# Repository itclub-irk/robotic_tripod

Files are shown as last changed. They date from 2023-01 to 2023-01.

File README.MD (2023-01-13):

# Роботизированный штатив

Данное устройство позволяет осуществлять наведение закрепленного на поворотном штативе прибора (камера, антенна, фонарь и т.д.) на портативный радиомаяк.

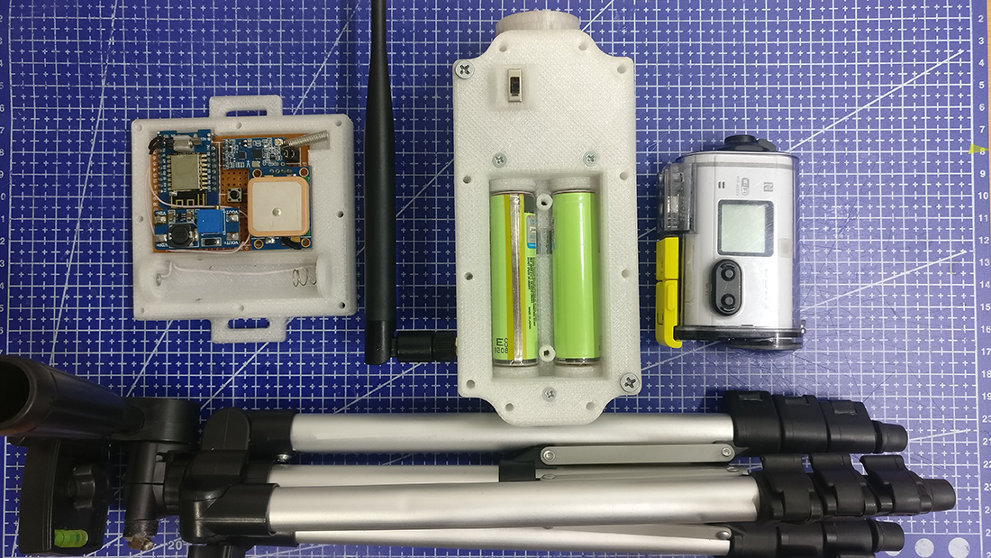
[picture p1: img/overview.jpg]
Внешний вид штатива


<details>
  <summary>Демонстрация работы штатива (18 Мб)</summary>

Демонстрация работы штатива

</details>

## Краткое описание конструкции

Штатив состоит из двух компонент - поворотный механизм и радиомаяк.

Радиомаяк определяет угловое положение относительно штатива при помощи ГНСС-приемника. Вычисленное значение при помощи беспроводного канала связи передаётся в поворотный механизм.

Поворотный механизм осуществляет поворот платформы с закрепленным прибором на требуемый угол.

## Варианты реализации

В данном репозитории представлен исходный код различных вариантов реализации роботизированного штатива.

Варианты поворотного механизма:

- С приводом платформы от сервопривода с PWM интерфейсом (Например SG90);
- С приводом от биполярного шагового двигателя NEMA с драйвером, поддерживающим интерфейс STEP/DIR (использовался двигатель NEMA17 и драйвер TMC2130);
- С приводом от униполярного шагового двигателя 28byj-48 и буфером ULN2003.
- С релейным трехпозиционным регулятором;
- С ПИД регулятором.

Варианты радиомаяка:

- С использованием библиотеки
  NeoGPS и аппаратного UART;
- С использованием библиотеки TinyGPS и программного UART для подключения к ГНСС-приёмнику;
- С использованием UART трансиверов HC-12 и программным контролем целостности пакетов;
- С использованием SPI трансиверов sx1278 на базе технологии LoRa и программным контролем целостности пакетов;
- С использованием UART трансиверов Ebyte E32-868T20S на базе технологии LoRa и аппаратным контролем целостности пакетов;
- Без внешних радиомодулей, с использованием AdHoc WiFi, UDP-датаграм и программным контролем целостности пакетов;
- Без внешних радиомодулей, с использованием протокола ESP-Now и программным контролем целостности пакетов;
- С обратной связью с поворотным механизмом;
- Без обратной связи с поворотным механизмом.

## Аппаратное обеспечение

Поворотный механизм (в зависимости от выбранного варианта реализации):

- WeMos D1 mini (ESP8266/ESP8266Ex);
- HC-12/SX1278/E32-868T20S
- Sg90/28byj-48/NEMA17
- ULN2003/TMC2130;
- Микропереключатель;
- Li-ION АКБ типоразмера 18650 (2 шт.);
- Понижающий DCDC преобразователь 8.2 ... 7.4 -> 5в;
- Внешняя штырьевая антенна на выбранный диапазон частот;
- Коаксиальный кабель с волновым сопротивлением 50 Ом и коннекторы для подключения кабеля к антенне и выбранному трансиверу.

Радиомаяк (В зависимости от выбранного варианта реализации):

- WeMos D1 mini (ESP8266/ESP8266Ex);
- HC-12/SX1278/E32-868T20S
- ГНСС-приемник NEO-6M с UART интерфейсом;
- Миниатюрный вибромотор;
- Li-ION АКБ типоразмера 18650 (1 шт.);
- Повышающий DCDC-преобразователь 4.2 ... 2.7 -> 5в. (Опционально);
- Микрокнопка без фиксации;
- Спиральная антенна на выбранный диапазон частот.

Электронные компоненты располагаются на макетных платах. Платы и остальные элементы размещаются в печатных корпусах. Файлы для печати находятся в каталоге _3d_.

<details>
  <summary>Образцы моделей для печати</summary>

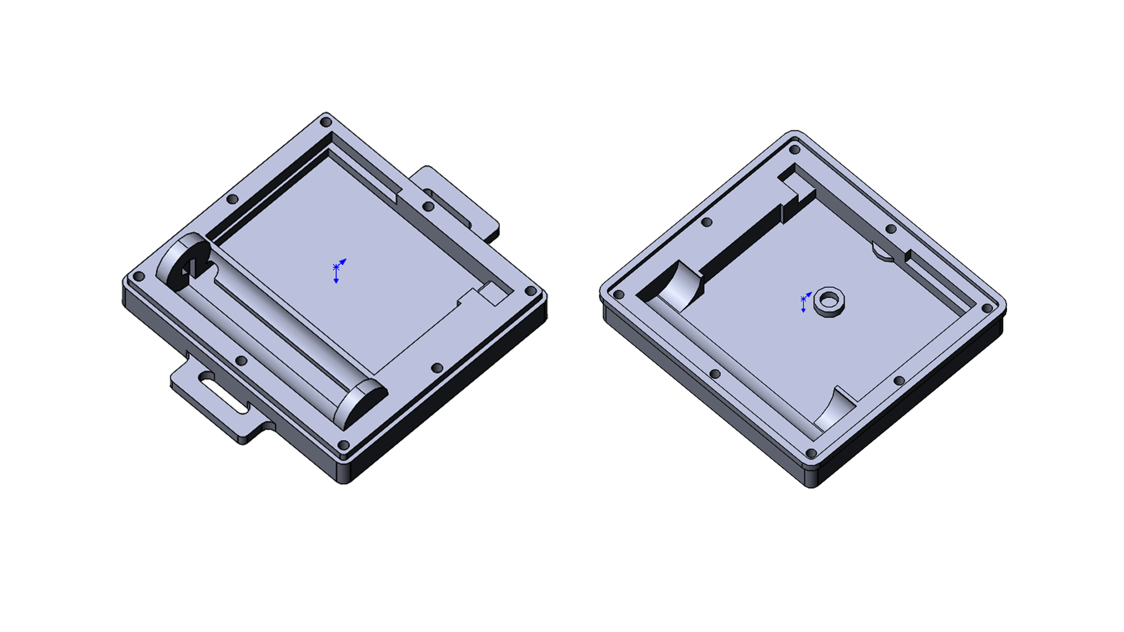
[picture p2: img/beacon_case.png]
Корпус радиомаяка

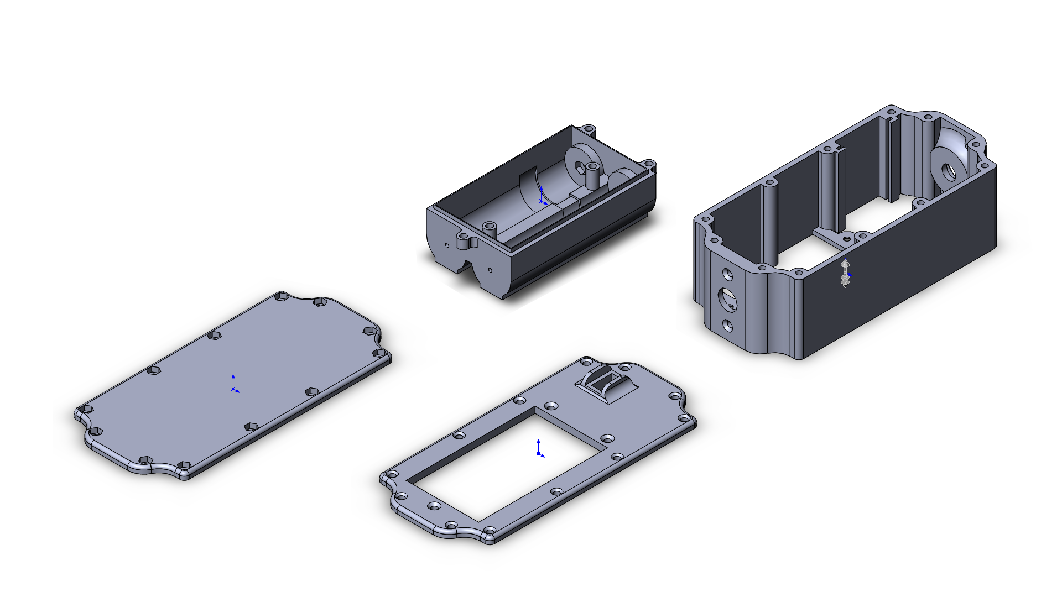
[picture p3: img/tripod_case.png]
Корпус поворотного механизма


</details>

## Программное обеспечение

Исходный код написан в среде Arduino IDE с расширением [Arduino core for ESP8266](https://github.com/esp8266/Arduino). В зависимости от выбранного варианта реализации необходимо установить следующие библиотеки:

- [LoRa](https://www.arduinolibraries.info/libraries/lo-ra);
- [TinyGPSPlus](https://github.com/mikalhart/TinyGPSPlus);
- [NeoGPS](https://www.arduinolibraries.info/libraries/neo-gps);
- [AccelStepper](https://www.arduinolibraries.info/libraries/accel-stepper);
- [CheapStepper](https://www.arduinolibraries.info/libraries/cheap-stepper);
- [ArduinoPIDLibrary](https://github.com/br3ttb/Arduino-PID-Library);
- [Ramp](https://github.com/siteswapjuggler/RAMP);
- [FastCRC](https://www.arduinolibraries.info/libraries/fast-crc).

## Краткое описание алгоритма работы

После включения питания поворотного механизма, производится автоматическое тестирование привода платформы. При этом она поворачивается на угол 90 градусов относительно первоначального положения по часовой и против часовой стрелки, после чего платформа должна вернутся в исходную позицию.

Радиомаяк после включения подаёт короткие сигналы при помощи вибромотора. Описание сигналов:

- Один короткий сигнал - отсутствует сигнал ГНСС, либо количество принимаемых спутников недостаточно для точного определения координат.
- Два коротких сигнала - отсутствует связь с поворотным механизмом (в случае использования варианта поворотного механизма с обратной связью);

Работа штатива возможна только после того, как включенный радиомаяк перестанет формировать короткие вибросигналы.

После того, как радиомаяк будет готов к работе, происходит фиксация в оперативной памяти радиомаяка координат поворотного механизма. Для этого, необходимо вплотную приблизится к поворотному механизму, и зажать кнопку радиомаяка до появления продолжительного вибросигнала (~1с.). После этого, необходимо указать радиомаяку вторую точку, для определения первоначального азимута поворотного механизма. Для этого необходимо отойти на расстояние около 10 метров от поворотного механизма и встать по центру кадра закрепленной на нем камеры (встать в фокус луча фонаря, антенны и т.п.) и зажать кнопку радиомаяка до появления продолжительного вибросигнала. После совершения данного действия, поворотный механизм будет автоматически удерживать радиомаяк в центре кадра установленной на нем камеры.

Определение координат радиомаяком осуществляется с частотой 5 Гц. Для перевода ГНСС-приемника в данный режим работы, при включении радиомаяка в приёмник передаётся предопределенная телеграма бинарного протокола UBX. Помимо этого, остальные телеграмы отключают неиспользуемые радиомаяком NMEA параметры (NMEA sentences): VTG, RMC, GSV. Данный шаг необходим, так как попытки перевести UART-порт ГНСС приемника на бодовую скорость, отличную от 9600 Бод/с. не увенчались успехом и использование "полновесного" NMEA протокола с частотой 5 Гц было бы невозможно.

После того, как определен первоначальный азимут поворотного механизма, радиомаяк 5 раз в секунду передаёт текущий горизонтальный угол относительно первоначального азимута. Для этого используется простейший ASCII-протокол, пакет которого имеет следующий вид: `@ANGLE@CRC@\n`, где ANGLE - текущий угол относительно первоначального азимута (целое число), CRC - контрольная сумма CRC8 от значения ANGLE (целое число). В некоторых вариантах реализации угол может быть вещественным числом, с точностью до одного знака после запятой, в этом случае параметр ANGLE - представляет собой значение угла, умноженное на 10.

Поворотный механизм, приняв пакет проверяет его целостность, если пакет принят корректно - определяется текущее значение ошибки как разность между фактическим углом поворота платформы относительно первоначального азимута и полученным углом от радиомаяка. Для определения фактического угла поворота платформы используется подсчет шагов шагового двигателя (количество шагов на один градус для двигателя указывается в переменной `STEPS_PER_DEGREE`). Алгоритм устранения ошибки зависит от выбранного варианта реализации. В простейшем случае происходит плавный поворот платформы в точку, где последний раз находился радиомаяк. Плавность разгона обеспечивается библиотекой AccelStepper. Во втором случае, управление шаговым двигателем выполняется с испльзованием PID-алгоритма, при этом, для исключения рывков, вызванных дискретностью получения координат от радиомаяка, используется сглаживание ошибки при помощи [ramp-функции](https://en.wikipedia.org/wiki/Ramp_function). Выходным значением PID-регулятора является интервал между шагами шагового двигателя. Полученный интервал используется в качестве уставки аппаратного таймера микроконтроллера, по прерыванию от которого совершается один шаг в нужном направлении.

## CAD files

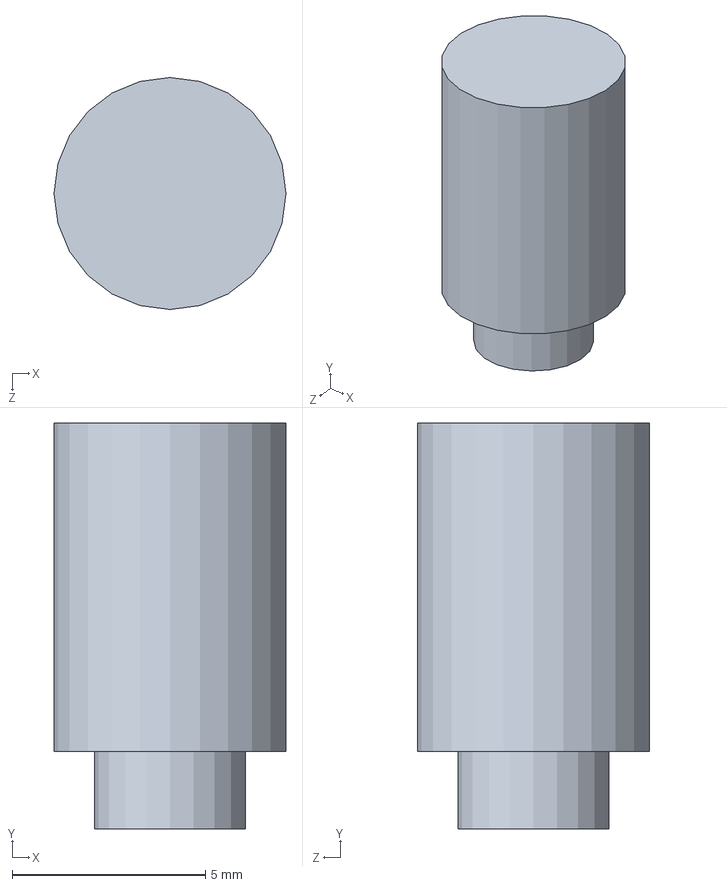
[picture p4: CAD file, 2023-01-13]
3d/beacon/v3/толкатель2.SLDPRT
6.00 x 10.5 x 6.00 mm

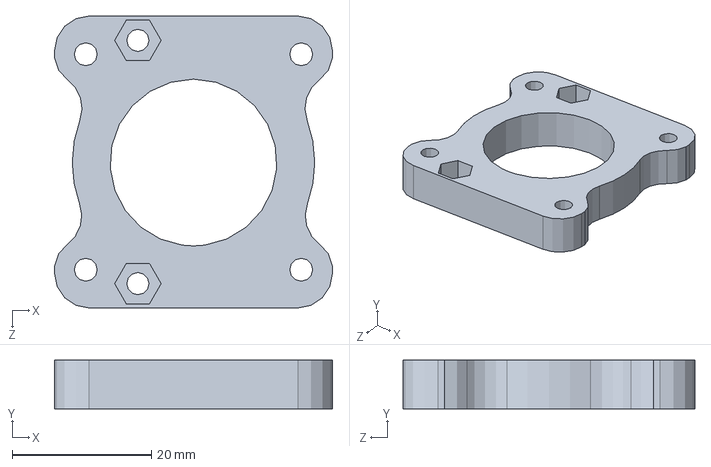
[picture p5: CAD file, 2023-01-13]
3d/tripod/v3/переходник nema17.SLDPRT
40.0 x 7.00 x 42.0 mm

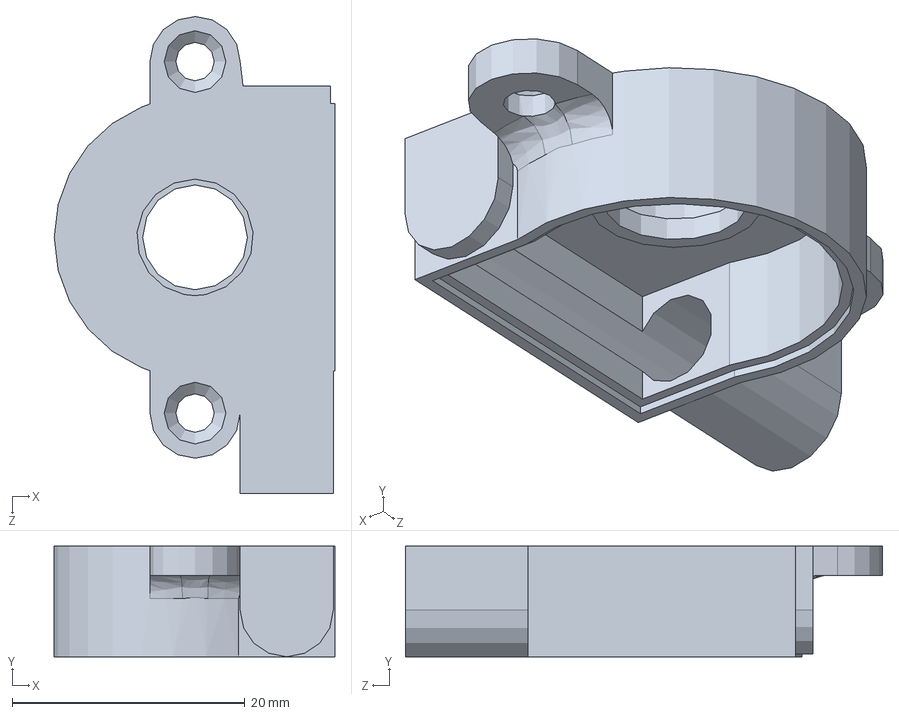
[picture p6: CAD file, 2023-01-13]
3d/tripod/датчик угла поворота/крышка1.SLDPRT
24.1 x 9.50 x 41.0 mm

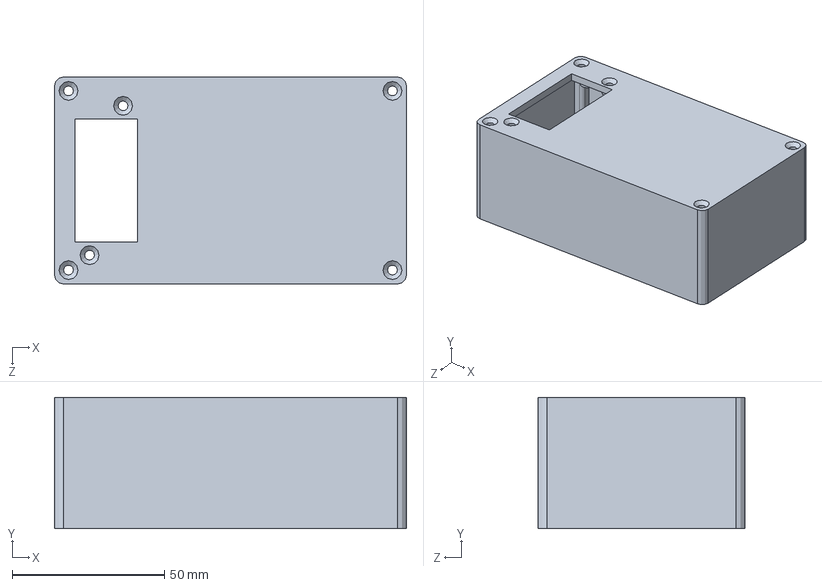
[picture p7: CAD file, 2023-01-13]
3d/tripod/основание корпуса.SLDPRT
115.5 x 43.0 x 68.0 mm

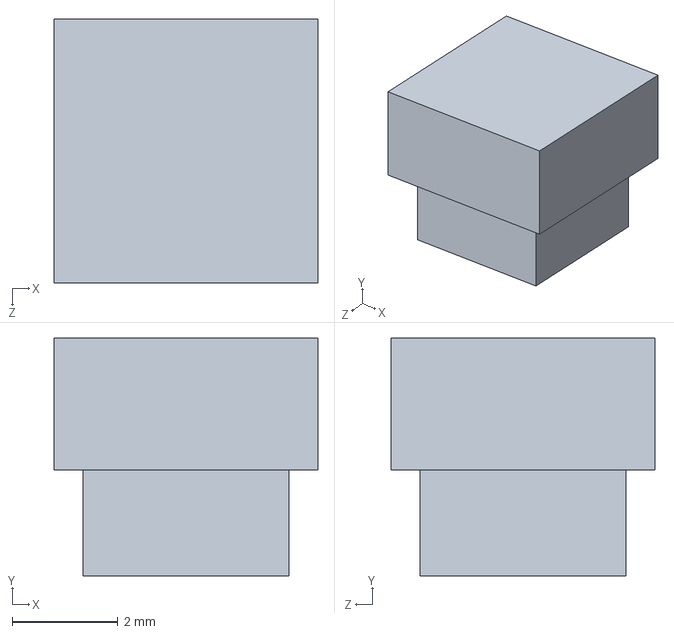
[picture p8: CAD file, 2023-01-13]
3d/beacon/v3/толкатель1.SLDPRT
5.00 x 4.50 x 5.00 mm

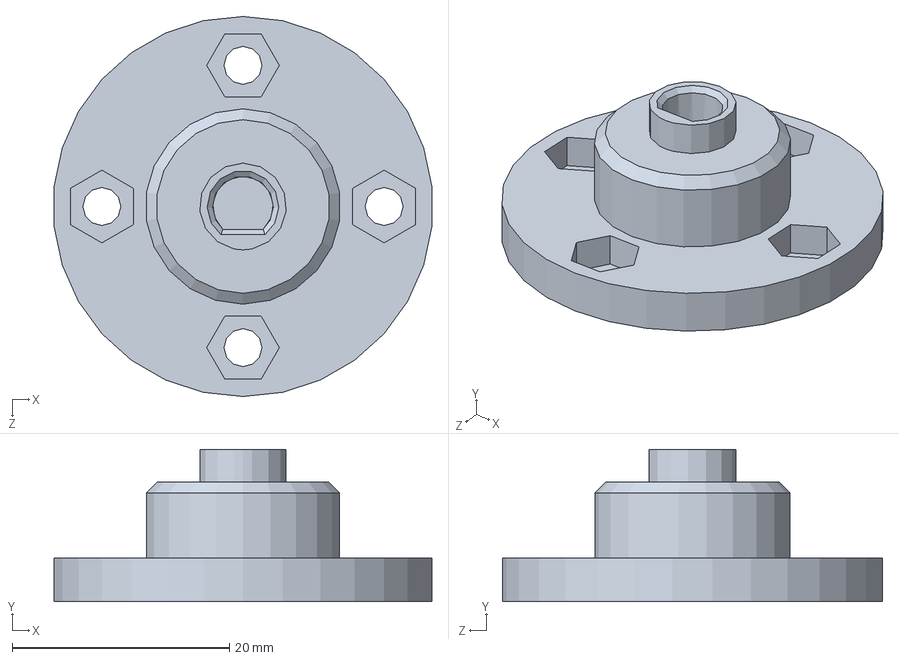
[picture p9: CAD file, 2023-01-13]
3d/tripod/v3/вал.SLDPRT
34.8 x 14.0 x 35.0 mm

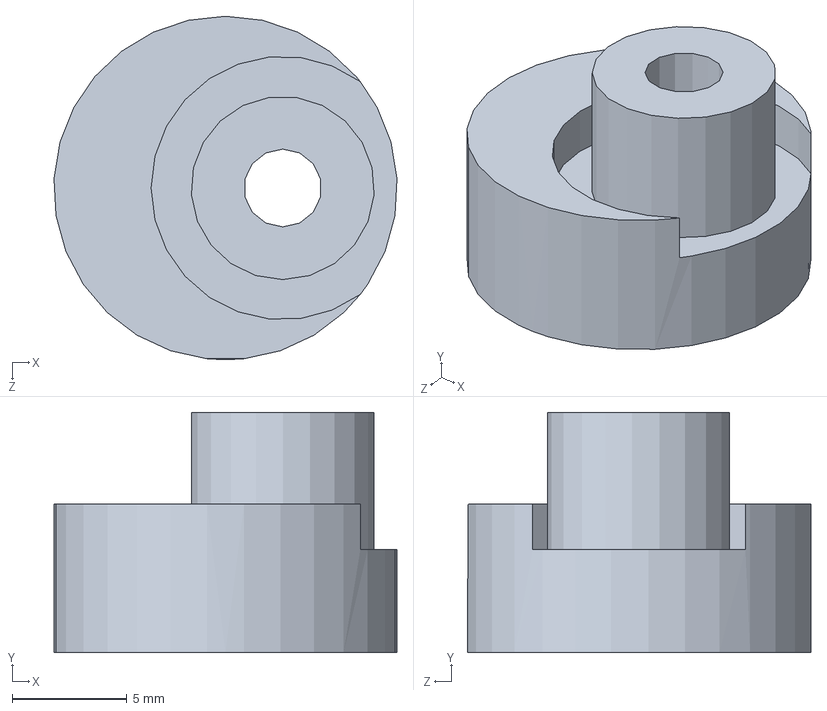
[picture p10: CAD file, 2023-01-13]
3d/tripod/датчик угла поворота/эксцентрик.SLDPRT
15.0 x 10.5 x 15.0 mm

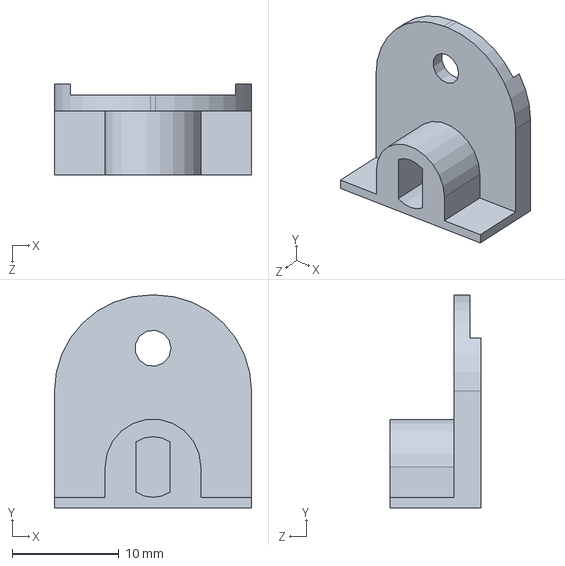
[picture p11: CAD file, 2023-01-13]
3d/tripod/Деталь3.SLDPRT
18.5 x 20.0 x 8.50 mm

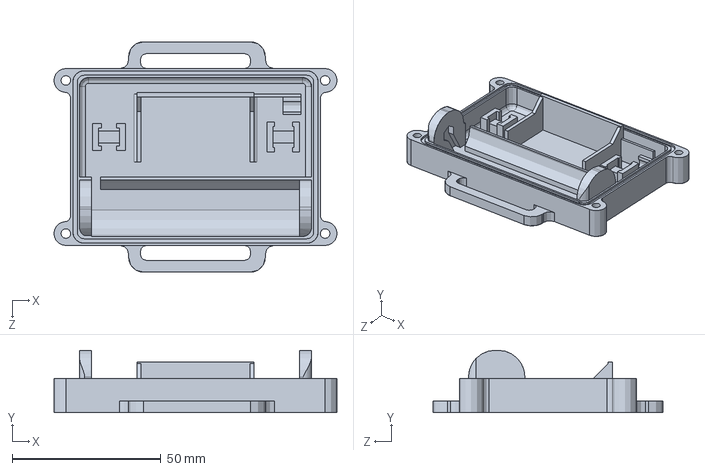
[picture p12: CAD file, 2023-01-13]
3d/beacon/v3/основание корпуса.SLDPRT
95.2 x 21.0 x 77.5 mm

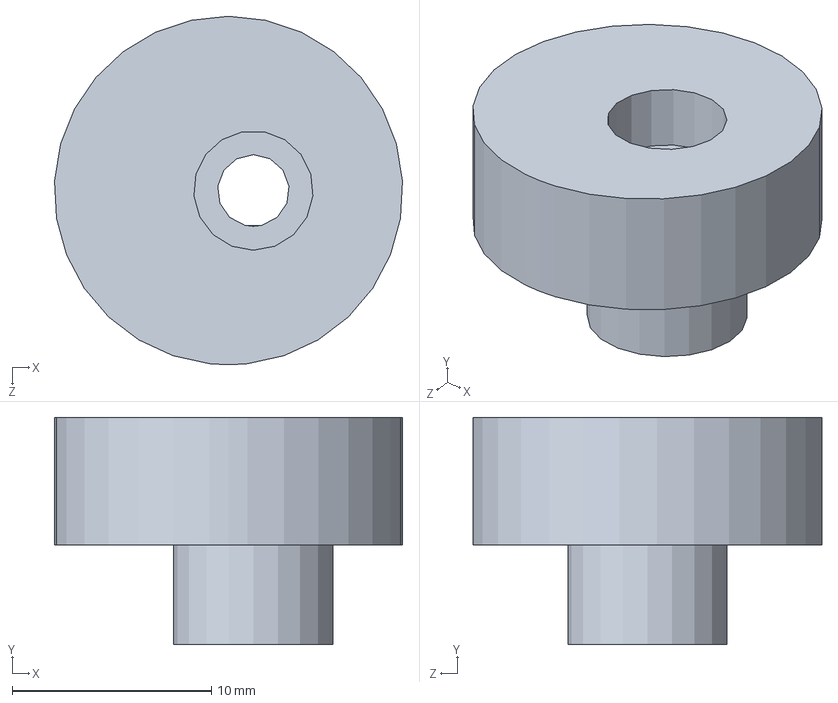
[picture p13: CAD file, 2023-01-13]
3d/tripod/датчик угла поворота/эксцентрик3.SLDPRT
17.5 x 11.4 x 17.5 mm

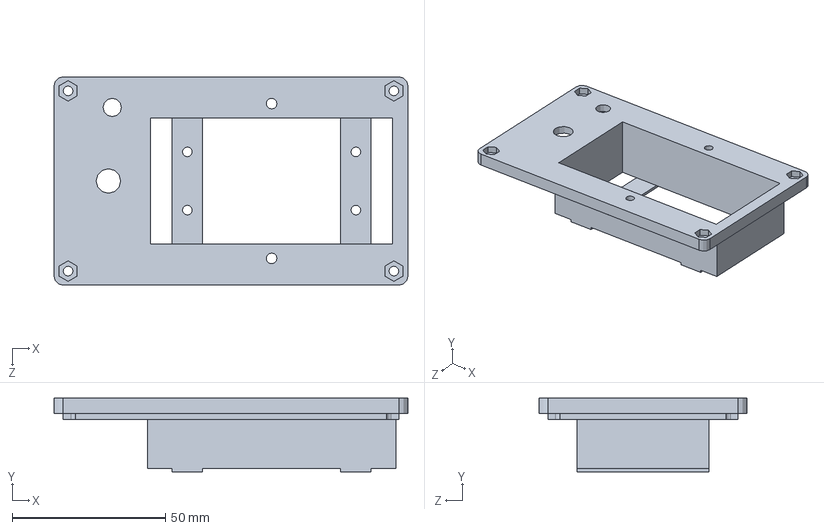
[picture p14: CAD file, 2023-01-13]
3d/tripod/крышка корпуса.SLDPRT
115.5 x 24.0 x 68.0 mm

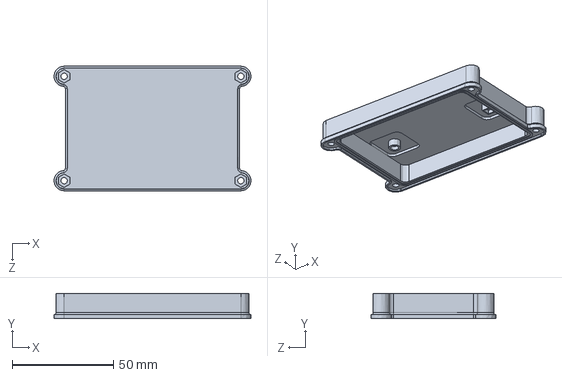
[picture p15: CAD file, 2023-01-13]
3d/beacon/v3/крышка корпуса.SLDPRT
97.2 x 12.5 x 61.5 mm

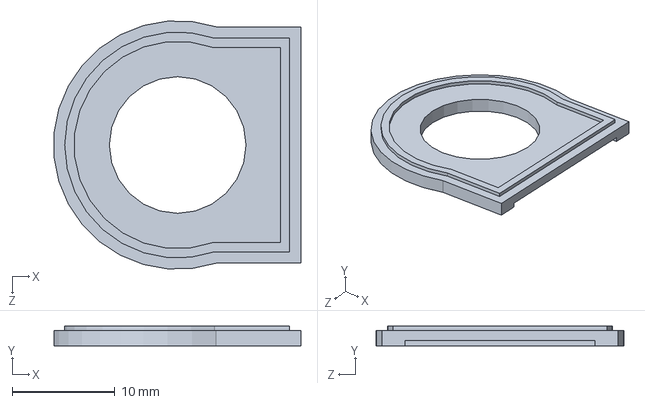
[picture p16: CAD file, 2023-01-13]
3d/tripod/датчик угла поворота/крышка2.SLDPRT
24.0 x 1.90 x 24.1 mm

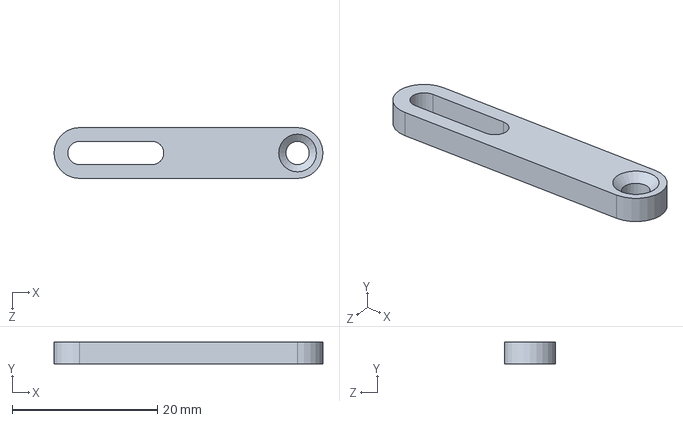
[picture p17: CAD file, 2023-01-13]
3d/tripod/Деталь1.SLDPRT
37.0 x 3.00 x 7.00 mm

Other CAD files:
3d/tripod/датчик угла поворота/эксцентрик4.SLDPRT
3d/tripod/Деталь2.SLDPRT
3d/tripod/gear2.stl
3d/tripod/датчик угла поворота/эксцентрик2.SLDPRT
3d/beacon/v1/крышка корпуса1.SLDPRT
3d/beacon/v1/крышка корпуса1.STL
3d/beacon/v1/крышка корпуса2.SLDPRT
3d/beacon/v1/крышка корпуса2.STL
3d/beacon/v1/прокладка.SLDPRT
3d/beacon/v2/держатель вибромотора.SLDPRT
3d/beacon/v2/держатель вибромотора.STL
3d/beacon/v2/крышка корпуса1.SLDPRT
3d/beacon/v2/крышка корпуса1.STL
3d/beacon/v2/крышка корпуса2.SLDPRT
3d/beacon/v2/крышка корпуса2.STL
3d/beacon/v2/пружина.SLDPRT
3d/beacon/v2/пружина.STL
3d/beacon/v2/толкатель.SLDPRT
3d/beacon/v2/толкатель.STL
3d/beacon/v3/крышка корпуса.STL
3d/beacon/v3/основание корпуса.STL
3d/beacon/v3/толкатель1.STL
3d/beacon/v3/толкатель2.STL
3d/tripod/gear1.stl
3d/tripod/v2/вал.SLDPRT
3d/tripod/v2/вал.STL
3d/tripod/v2/вал2.SLDPRT
3d/tripod/v2/вал2.STL
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

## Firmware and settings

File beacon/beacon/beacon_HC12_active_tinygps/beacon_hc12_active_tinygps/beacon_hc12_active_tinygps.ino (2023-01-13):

#include <ESP8266WiFi.h>
#include <SoftwareSerial.h>
#include <TinyGPS++.h>

#define BUTTON_PIN 4
#define POWER_ON_PIN 5
#define VIB_PIN 0
#define radioSerial Serial

static const int RXPin = 14, TXPin = 12;
static const uint32_t GPSBaud = 9600;
const uint32_t COMMAND_DELAY = 250;
TinyGPSPlus gps;

SoftwareSerial gpsPort(RXPin, TXPin); //Rx-D5, Tx-D6

unsigned long buttonPressedMillis = 0;
unsigned long powerOffPressedMillis = 0;
int buttonInterval = 1000;
int powerOffInterval = 3000;

boolean beaconEnabled = false;
boolean lastButtonState = false;
boolean actionFired = false;

int ledState = HIGH;
unsigned long ledOnMillis = 0;
const long interval = 1000;

String lastSendedMessage = "";
long lastMessageMillis = 0;
long sendMessageInterval = 200;

double defaultAngle;

double beaconLat;
double beaconLong;

double tripodLat;
double tripodLong;

double checkpointLat;
double checkpointLong;

double defaultAzimuth;
double beaconAzimuth;
double angle;

const int HEARTBEAT_INTERVAL = 3000;

boolean heartbeatReceived;
boolean gpsReceived;
unsigned long lastHeartbeatCheckMillis;

double divider = 10000000;

const unsigned char ubxRate5Hz[] PROGMEM =
  { 0x06,0x08,0x06,0x00,200,0x00,0x01,0x00,0x01,0x00 };

const unsigned char ubxDisableVTG[] PROGMEM =
  { 0x06,0x01,0x08,0x00,0xF0,0x05,0x00,0x00,0x00,0x00,0x00,0x01 };

const unsigned char ubxDisableRMC[] PROGMEM =
  { 0x06,0x01,0x08,0x00,0xF0,0x04,0x00,0x00,0x00,0x00,0x00,0x01 };

const unsigned char ubxDisableGSV[] PROGMEM =
  { 0x06,0x01,0x08,0x00,0xF0,0x03,0x00,0x00,0x00,0x00,0x00,0x01 };

static const uint8_t PROGMEM dscrc_table[] = {
    0, 94,188,226, 97, 63,221,131,194,156,126, 32,163,253, 31, 65,
  157,195, 33,127,252,162, 64, 30, 95,  1,227,189, 62, 96,130,220,
   35,125,159,193, 66, 28,254,160,225,191, 93,  3,128,222, 60, 98,
  190,224,  2, 92,223,129, 99, 61,124, 34,192,158, 29, 67,161,255,
   70, 24,250,164, 39,121,155,197,132,218, 56,102,229,187, 89,  7,
  219,133,103, 57,186,228,  6, 88, 25, 71,165,251,120, 38,196,154,
  101, 59,217,135,  4, 90,184,230,167,249, 27, 69,198,152,122, 36,
  248,166, 68, 26,153,199, 37,123, 58,100,134,216, 91,  5,231,185,
  140,210, 48,110,237,179, 81, 15, 78, 16,242,172, 47,113,147,205,
   17, 79,173,243,112, 46,204,146,211,141,111, 49,178,236, 14, 80,
  175,241, 19, 77,206,144,114, 44,109, 51,209,143, 12, 82,176,238,
   50,108,142,208, 83, 13,239,177,240,174, 76, 18,145,207, 45,115,
  202,148,118, 40,171,245, 23, 73,  8, 86,180,234,105, 55,213,139,
   87,  9,235,181, 54,104,138,212,149,203, 41,119,244,170, 72, 22,
  233,183, 85, 11,136,214, 52,106, 43,117,151,201, 74, 20,246,168,
  116, 42,200,150, 21, 75,169,247,182,232, 10, 84,215,137,107, 53};

void sendUBX( const unsigned char *progmemBytes, size_t len ){
  gpsPort.write( 0xB5 ); // SYNC1
  gpsPort.write( 0x62 ); // SYNC2

  uint8_t a = 0, b = 0;
  while (len-- > 0) {
    uint8_t c = pgm_read_byte( progmemBytes++ );
    a += c;
    b += a;
    gpsPort.write( c );
  }

  gpsPort.write( a ); // CHECKSUM A
  gpsPort.write( b ); // CHECKSUM B

}

uint8_t crc8(const uint8_t *addr, uint8_t len) {
  uint8_t crc = 0;
  while (len--) {
    crc = pgm_read_byte(dscrc_table + (crc ^ *addr++));
  }
  return crc;
}

double toRadians(double angle) {
  return (angle * 71) / 4068;
}

double toDegrees(double angle) {
  return (angle * 4068) / 71;
}

double getAzimuth(double p1lat, double p1long, double p2lat, double p2long) {
  p1lat = toRadians(p1lat);
  p1long = toRadians(p1long);
  p2lat = toRadians(p2lat);
  p2long = toRadians(p2long);

  double delta_long = p2long - p1long;
  double y = sin(delta_long) * cos(p2lat);
  double x = cos(p1lat) * sin(p2lat) - sin(p1lat) * cos(p2lat) * cos(delta_long);
  double a = atan2(y, x);
  a = toDegrees(a);

  if (a < 0) {
    return a + 360;
  } else {
    return a;
  }
}

void initVariables(){
  lastSendedMessage = "";
  lastMessageMillis = 0;
  sendMessageInterval = 200;

  defaultAngle = 0;

  beaconLat = 0;
  beaconLong = 0;

  tripodLat = 0;
  tripodLong = 0;

  checkpointLat = 0;
  checkpointLong = 0;

  defaultAzimuth = 0;
  beaconAzimuth = 0;
  angle = 0;
  
  heartbeatReceived = false;
  gpsReceived = false;
  lastHeartbeatCheckMillis = 0;  
}

void setup(){
  pinMode(BUTTON_PIN, INPUT_PULLUP);
  pinMode(POWER_ON_PIN, OUTPUT);
  digitalWrite(POWER_ON_PIN, LOW); 
  
  pinMode(VIB_PIN, OUTPUT);
  digitalWrite(VIB_PIN, LOW); 
   
  Serial.begin(9600);
  gpsPort.begin(9600);

  pinMode(LED_BUILTIN, OUTPUT);
  digitalWrite(LED_BUILTIN, ledState);
  lastHeartbeatCheckMillis = millis();

  initVariables();
  WiFi.forceSleepBegin();
  delay(1);  
}

void initExternalDevices(){
  sendUBX(ubxRate5Hz, sizeof(ubxRate5Hz));  
  delay(COMMAND_DELAY);
  sendUBX(ubxDisableVTG, sizeof(ubxDisableVTG));
  delay(COMMAND_DELAY);
  sendUBX(ubxDisableRMC, sizeof(ubxDisableRMC));  
  delay(COMMAND_DELAY);
  sendUBX(ubxDisableGSV, sizeof(ubxDisableGSV)); 
}

void loop(){
  handleButton();

  if(beaconEnabled){
    handleGPS();
    handleHeartbeat(); 
  }
}

void handleButton() {
  boolean currentButtonState = !digitalRead(BUTTON_PIN);
  
  if (currentButtonState && !lastButtonState) {
    buttonPressedMillis = millis();
    powerOffPressedMillis = millis();
    
    lastButtonState = currentButtonState;
  };
  if (!actionFired && currentButtonState && (millis() - buttonPressedMillis) >= buttonInterval) {
    ledState = LOW;
    digitalWrite(LED_BUILTIN, LOW);
    digitalWrite(VIB_PIN, HIGH);
    
    ledOnMillis = millis();
    handleCheckpoint();
    actionFired = true;
  };

//  power on / off
  if(currentButtonState && (millis() - powerOffPressedMillis) >= powerOffInterval){
    flashLED(3, 200);
    if(beaconEnabled){
      digitalWrite(POWER_ON_PIN, LOW); 
      beaconEnabled = false;     
    }else{
      digitalWrite(POWER_ON_PIN, HIGH);
      initVariables();
      delay(100);
      initExternalDevices();
      beaconEnabled = true;
    };
  };

  if (!currentButtonState && lastButtonState) {
    lastButtonState = currentButtonState;        
    actionFired = false;
  };

  if (ledState == LOW) {
    unsigned long currentMillis = millis();
    if (currentMillis - ledOnMillis >= interval) {
      ledState = HIGH;
      digitalWrite(LED_BUILTIN, ledState);
      digitalWrite(VIB_PIN, LOW);      
    }
  }
}

void flashLED(int times, long period){
  for(int i = 0; i < times; i++){
    digitalWrite(LED_BUILTIN, LOW);
    digitalWrite(VIB_PIN, HIGH);
    delay(period);
    digitalWrite(LED_BUILTIN, HIGH);
    digitalWrite(VIB_PIN, LOW);
    delay(period);
  } 
}

void handleCheckpoint() {
  if (tripodLat == 0 && tripodLong == 0) {
    tripodLat = beaconLat;
    tripodLong = beaconLong;
  } else if (checkpointLat == 0 && checkpointLong == 0) {
    checkpointLat = beaconLat;
    checkpointLong = beaconLong;
    if (tripodLat != 0 && tripodLong != 0 && defaultAzimuth == 0) {
      defaultAzimuth = getAzimuth(tripodLat, tripodLong, checkpointLat, checkpointLong);
    }
  }
}

static void handleGPS() {
  while (gpsPort.available() > 0){
    gps.encode(gpsPort.read());
    if (gps.location.isUpdated()){
      gpsReceived = true;
      beaconLat = gps.location.lat();
      beaconLong = gps.location.lng();
      handleBeaconCoordinates();
    };
  };
}

double modulo(double a, double b) {
  return a - floor(a / b) * b;
}

void handleBeaconCoordinates() {
  if (tripodLat != 0 && tripodLong != 0 && checkpointLat != 0 && checkpointLong != 0) {
    beaconAzimuth = getAzimuth(tripodLat, tripodLong, beaconLat, beaconLong);

    angle = beaconAzimuth - defaultAzimuth;
//    angle = modulo(angle + 180, 360) - 180;
    angle = modulo(angle, 360);
    lastSendedMessage = String(round(truncate(angle, 1) * 10));
    sendMessage(lastSendedMessage);
  }
}

void handleMessage(){
  if(lastSendedMessage != "" && (millis() - lastMessageMillis) >= sendMessageInterval){
    sendMessage(lastSendedMessage);
    lastMessageMillis = millis();
  }  
}

static void sendMessage(String msg) {
  String m;
  m = '@' + msg + '@' + hashData(msg) + '\n';
  radioSerial.println(m);
}

String hashData(String data) {
  return String(crc8((const uint8_t*)data.c_str(), data.length()));
}

void handleHeartbeat(){
  if(radioSerial.available() > 0){
    heartbeatReceived = true;
    while (radioSerial.available() > 0) {
      radioSerial.read();
    };    
  };

  if((millis() - lastHeartbeatCheckMillis ) >= HEARTBEAT_INTERVAL){
    if(heartbeatReceived){
      heartbeatReceived = false;
      if(gpsReceived){
        gpsReceived = false;
      }else{
        flashLED(1, 100);  
      };
    }else{
      flashLED(2, 100);
    };

    lastHeartbeatCheckMillis  = millis();
  }       
}

double truncate(double val, byte dec)
{
    double x = val * pow(10, dec);
    double y = round(x);
    double z = x - y;
    if ((int)z == 5)
    {
        y++;
    } else {}
    x = y / pow(10, dec);
    return x;
}

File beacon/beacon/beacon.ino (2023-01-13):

#include <NMEAGPS.h>
#include <ESP8266WiFi.h>

#define gpsPort Serial
#define DEBUG_PORT Serial
#define USING_GPS_PORT "Serial"
#define GPS_PORT_NAME "Serial"
#define BUTTON_PIN 5
#include <Streamers.h>
static NMEAGPS  gps;
static gps_fix  fix;
const char *ssid = "tripod";
const char *password = "tripodtripod";

boolean lastButtonState = false;

static void sendButtonData(){
  WiFiClient client;
  const char * host = "192.168.4.1";
  const int httpPort = 80;
  
  if (!client.connect(host, httpPort)) {
    Serial.println("connection failed");
    return;
  }

  String url = "/button/";

  client.print(String("GET ") + url + " HTTP/1.1\r\n" +
               "Host: " + host + "\r\n" +
               "Connection: close\r\n\r\n");
  unsigned long timeout = millis();
  while (client.available() == 0) {
    if (millis() - timeout > 5000) {
      Serial.println(">>> Client Timeout !");
      client.stop();
      return;
    }
  }      
}

static void sendGPSData()
{
  double divider = 10000000;

//  trace_all( DEBUG_PORT, gps, fix );
  DEBUG_PORT.println(' ');
  DEBUG_PORT.print("Lat as long: ");
  DEBUG_PORT.println(fix.latitudeL());
  DEBUG_PORT.print("Lat as float: ");
  printDouble(fix.latitudeL() / divider, 7);
  Serial.println(" ");

  DEBUG_PORT.print("Long as long: ");
  DEBUG_PORT.println(fix.longitudeL());
  DEBUG_PORT.print("Long as float: ");
  printDouble(fix.longitudeL() / divider, 7);  
  Serial.println(" ");

  WiFiClient client;
  const char * host = "192.168.4.1";
  const int httpPort = 80;

  if (!client.connect(host, httpPort)) {
    Serial.println("connection failed");
    return;
  }

  // We now create a URI for the request. Something like /data/?sensor_reading=123
  String url = "/beacon/";
  url += "?lat=";
  url += fix.latitudeL();
  url += "&long=";
  url += fix.longitudeL();

  client.print(String("GET ") + url + " HTTP/1.1\r\n" +
               "Host: " + host + "\r\n" +
               "Connection: close\r\n\r\n");
  unsigned long timeout = millis();
  while (client.available() == 0) {
    if (millis() - timeout > 5000) {
      Serial.println(">>> Client Timeout !");
      client.stop();
      return;
    }
  }  
} 

void printDouble( double val, byte precision){
 Serial.print (int(val));  //prints the int part
 if( precision > 0) {
   Serial.print("."); // print the decimal point
   unsigned long frac;
   unsigned long mult = 1;
   byte padding = precision -1;
   while(precision--)
      mult *=10;
      
   if(val >= 0)
     frac = (val - int(val)) * mult;
   else
     frac = (int(val)- val ) * mult;
   unsigned long frac1 = frac;
   while( frac1 /= 10 )
     padding--;
   while(  padding--)
     Serial.print("0");
   Serial.print(frac,DEC) ;
 }
}

static void GPSloop()
{
  while (gps.available( gpsPort )) {
    fix = gps.read();
    sendGPSData();
  }

} 

void handleButton(){
  boolean currentButtonState = !digitalRead(BUTTON_PIN);
  if(currentButtonState && !lastButtonState){
    lastButtonState = true;
    sendButtonData();
  }else if(!currentButtonState && lastButtonState){
    lastButtonState = false; 
  }
}

void setup()
{
  DEBUG_PORT.begin(9600);
  while (!DEBUG_PORT);
  DEBUG_PORT.flush();

  pinMode(BUTTON_PIN, INPUT_PULLUP);

  gpsPort.begin( 9600 );

  WiFi.mode(WIFI_STA);
  WiFi.begin(ssid, password);

  while (WiFi.status() != WL_CONNECTED) {
    delay(500);
  }  
}

void loop()
{
  GPSloop();
  handleButton();  
}
